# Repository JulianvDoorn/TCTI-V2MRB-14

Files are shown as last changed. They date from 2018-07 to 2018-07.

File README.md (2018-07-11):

# Tri-Servo Platform Practicum
De scope van dit practicum richt zich op het controleren van de positie van een bal in een 2D ruimte. Deze 2D ruimte stelt een plaat voor wat aan de hand van servomotoren kan worden gekanteld. Aan de hand van PID worden de graden berekend en kan er een erg precies systeem worden ontwikkeld.

Het lokaliseren van de bal op de platform zal worden gedaan met gebruik van een webcam. Deze webcam staat op een statief gemonteerd en is haaks op het  _tri-servo platform_  gericht. Dan kan er aan de hand van vision algoritmes de bal worden herkend.

Dit past goed bij de cursus  _Meten, regelen en besturen_, want alle drie de aspecten komen voor in dit practicum. (Meten: vision algoritme, regelen: PID berekening, besturen: servo motoren)

## Functionality
De functionaliteit van de hard- en software staan hieronder beschreven, deze zijn afgeleid uit de MoSCoW requirements in het PvA:

> Cijfers representeren een item uit de must, should and could have. De tientallen representeren de categorie (must, should of could). De eenheden vormen een feature. Voor een werkbaar product is elke feature naar minimaal 'must have' niveau worden gebracht.

-   **21 - Vlugge PID**  PID integratie met een vlugge afstelling, de bal komt snel dichtbij. De steady state error detection (integraal) zal uiteindelijk de laatste correctie doen.
-   **12 - Bal detectie**  Vision algoritme voor bal detectie.
-   **13 - Error bepaling**  Error bepaling op drie assen. Het platform kent drie motoren, dus voor elke motor moet er een error worden bepaald om PID te kunnen regelen.
-   **34 - Automatische beeldafkapping**  Automatische beeldafkapping van de webcam tijdens opstarten.
-   **35 - Automatische motor lokalisatie**  Automatische lokalisering van de motors tijdens opstarten.
-   **26 - Handmatige SetPoint**  Handmatig ingestelde SetPoint, de gebruiker kan op een venster klikken waar de SetPoint is.
-   **17 - Servo aansturing**  Het systeem kan aan de hand van actuators de bal in een richting kunnen bewegen.

## Required Hardware

- 'Tri-Servo Platform'
	- Drie krachtig genoege servomotoren
	- Lichte plaat met lokalisatiestickers (40x40 plexiglas, bijvoorbeeld, liefst ondoorzichtig d.m.v. tape of verf)
	- Elastiek waarmee de plaat in het midden mee wordt gehouden
	- Juiste voeding voor de servomotoren (Wij werkten met een 5V, 0.7A telefoonoplader)
> 5V kan door de Arduino worden geleverd, maar soms trokken de servos te veel stroom, waardoor de Arduino zich resette. Dit is vervelend wanneer je een bal probeert te balanceren.
- Arduino Due
- USB Webcam
	- Statief voor de webcam wat hoog genoeg is om de gehele Tri-Servo Platform in beeld te brengen

### Pin Layout Diagram

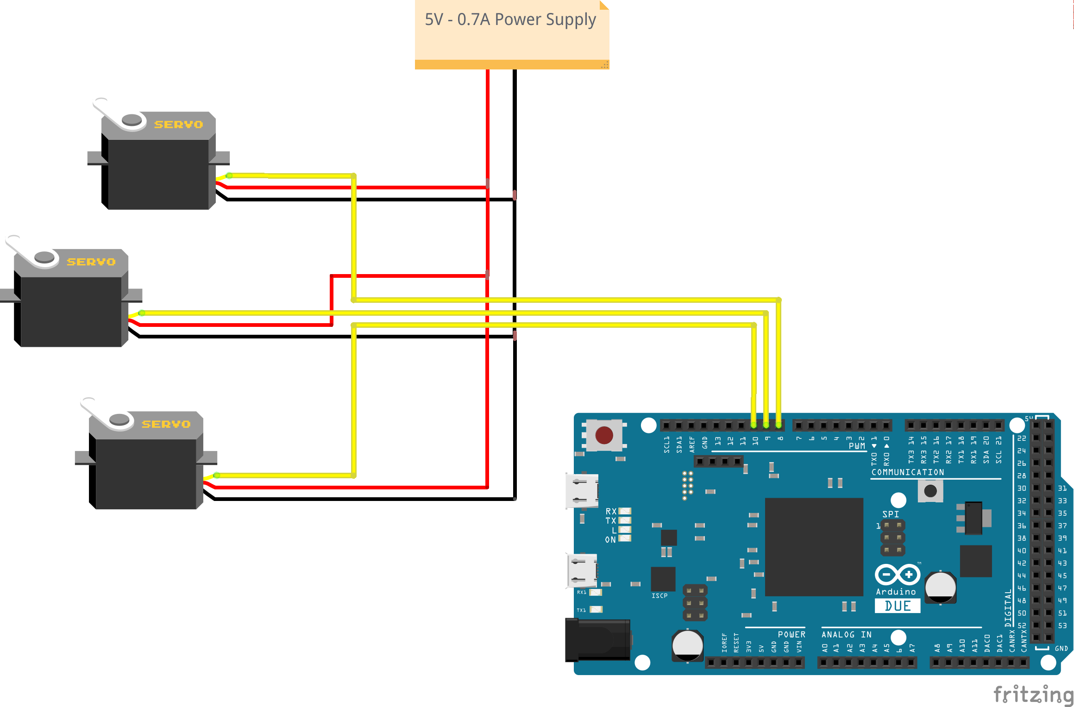
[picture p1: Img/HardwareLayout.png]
Drie Servos en Arduino
<br>
<sub>Pinlayout</sub>

In het bovenstaande diagram staat beschreven hoe de Arduino Due is verbonden met de drie servomotoren en hoe de servomotoren aan de voeding is aangesloten.

Het staat niet gemodelleerd in het schema maar de Arduino krijgt zijn voeding van de PC doormiddel van een USB. Tevens wordt er met deze USB verbinding gecommuniceerd met de PID software. Overigens moet de USB webcam ook aangesloten zijn aan de PC.

## Software dependencies

- Arduino IDE/Toolchain
- Python 3
- OpenCV (voor Python 3)
- Numpy

### Install and user Guide

Wanneer alle hardware gereed staat, kan de software worden geïnstalleerd. De software is doet in principe heel veel zelf wanneer de webcam op het bewegende platform staat gericht. Het is belangrijk dat alle stickers herkenbaar voor de webcam zijn.

#### Vision
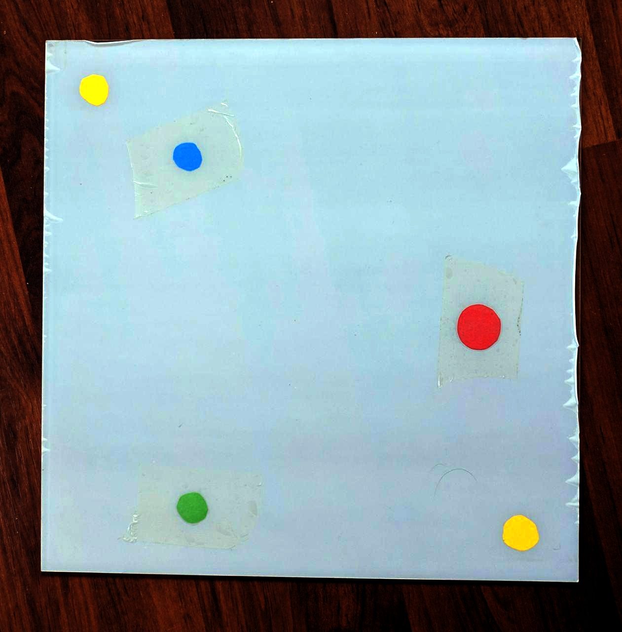
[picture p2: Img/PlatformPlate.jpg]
Platform met stickers
<br>
<sup>Foto van de plaat, hoe de webcam het zou moeten zien</sup>

Dit is hoe onze plaat eruit ziet voor onze webcam. Het is van belang dat de stickers rond zijn en gekleurd in dezelfde kleuren als hierboven. De software filtert namelijk alle kleuren eruit behalve, bijvoorbeeld, rood. Wanneer dit is gedaan voert het stickerherkenning uit. 

De webcam moet verbonden zijn met de 1<sup>e</sup> (niet de 0<sup>e</sup>) virtuele webcam poort. Dit kan in main.py worden aangepast bij `cap = cv2.VideoCapture(1)`. Dit komt omdat de laptop waar het al op was ontwikkeld een webcam op de 0<sup>e</sup> webcam heeft.

#### Arduino
Voordat het allemaal werkt moet eerst nog de Arduino worden geflashed met de code dat de servomotoren aanstuurd aan de hand van seriele commando's. De sketch kan je vinden in het mapje `Arduino/`. Deze sketch kan je met de Arduino IDE uploaden naar je Arduino. Wanneer dit is gedaan heb je de Arduino IDE niet meer nodig.

### Class Diagram

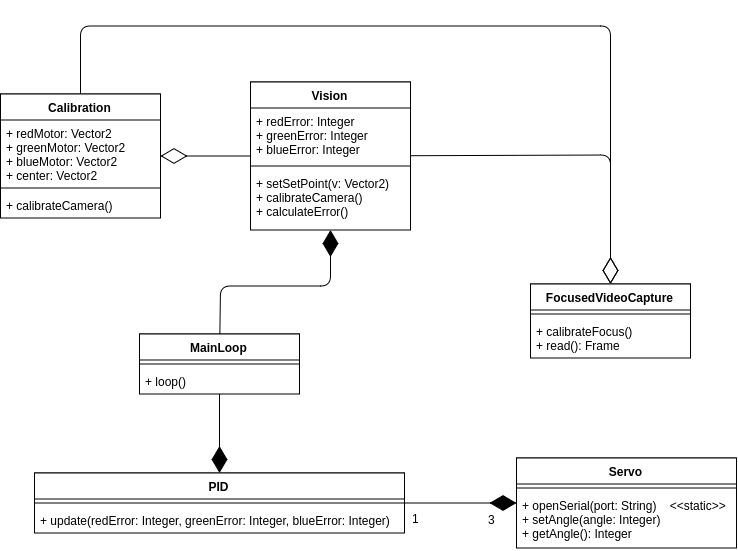
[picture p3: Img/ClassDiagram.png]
Class diagram
<br>
<sup>Klassediagram van de Python software</sup>

| Element | Description |
| :---: |---|
| Vision Class | Dit is het metende gedeelde van het systeem. Het gebruik verschillende algoritmes en een instantie van Calibration om errors te berekenen die bruikbaar zijn voor een PID regelaar. |
| Calibration Class | Bevat subroutines om aan de hand van een video stream de motors te lokaliseren en een middelpunt te berekenen. Wanneer een instantie zich heeft gekalibreerd kan een instantie van Vision gebruik maken van de kalibratie. |
| FocusedVideoCapture Class | Dit is een wrapper class de VideoCapture uit OpenCV. Deze class runt nog een _crop_ operatie over de frame die uit VideoCapture.read() komt. Dit is bruikbaar voor het optimaliseren van de vision algoritmes.  |
| PID Class | Dit is het regelende component van dit systeem. Instances van PID kennen drie servo's en bevat een 'update' functie die de servo's update aan de hand van de ontvangen errors. |
| Servo Class | Dit is het regelende deel van het systeem. Het is gespecialiseerd voor het sturen van commando's naar de Arduino. Elke servo instance bestuurd maar een servo, maar de daadwerkelijke controller kent er maar liefst drie. Daarom moet er de seriële verbinding tussen instances worden gedeeld. Tenzij het geëxpliciteerd is dat verschillende servo's andere seriële poorten gebruiken. |
| MainLoop | In de daadwerkelijke software, is MainLoop niet een class. Maar voor het nut van een class diagram was het belangrijk om dit component de modelleren. Het nut van de MainLoop is om het PID gedeelte en het Vision gedeelte samen te voegen. |

### PID Loop

PID Feedback Loop<br>
<sup>Diagram van de PID feedback lus</sup>

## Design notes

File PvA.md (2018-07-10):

# PvA Tri-Servo Platform Practicum
De scope van dit practicum richt zich op het controleren van de positie van een bal in een 2D ruimte. Deze 2D ruimte stelt een plaat voor wat aan de hand van servomotoren kan worden gekanteld. Aan de hand van PID worden de graden berekend en kan er een erg precies systeem worden ontwikkeld.

Het lokaliseren van de bal op de platform zal worden gedaan met gebruik van een webcam. Deze webcam staat op een statief gemonteerd en is haaks op het _tri-servo platform_ gericht. Dan kan er aan de hand van vision algoritmes de bal worden herkend.

Dit past goed bij de cursus _Meten, regelen en besturen_, want alle drie de aspecten komen voor in dit practicum. (Meten: vision algoritme, regelen: PID berekening, besturen: servo motoren)

## MoSCoW
### Must have
- __11 - Werkbare PID__ PID integratie met werkbare afstelling waarbij de bal uiteindelijk wel op zijn plek komt
- __12 - Bal detectie__ Vision algoritme voor bal detectie.
- __13 - Error bepaling__ Error bepaling op drie assen. Het platform kent drie motoren, dus voor elke motor moet er een error worden bepaald om PID te kunnen regelen.
- __14 - Hardcoded beeldafkapping__ De focus frame van de webcam zit altijd op dezelfde plek. De focus frame zorgt ervoor dat de vision algoritmes optimaal presteren.
- __15 - Hardcoded motor lokalisatie__ Motor posities zitten altijd op dezelfde plek.
- __16 - Hardcoded SetPoint__ Het systeem wilt de bal altijd naar het midden toe brengen.
- __17 - Servo aansturing__ Het systeem moet aan de hand van actuators de bal in een richting kunnen bewegen.
### Should have
- __21 - Vlugge PID__ PID integratie met een vlugge afstelling, de bal komt snel dichtbij. De steady state error detection (integraal) zal uiteindelijk de laatste correctie doen.
- __24 - Handmatige beeldafkapping__ Handmatig ingestelde beeldafkapping van de webcam on de vision algoritmes optimaal te laten werken. Bij opstarten wordt het vlak door de gebruiker ingevoerd.
- __25 - Handmatige motor lokalisatie__ Handmatig ingestelde motor posities relatief aan het focuspunt van de webcam. Bij opstarten worden de punten door de gebruiker ingevoerd.
- __26 - Handmatige SetPoint__ Handmatig ingestelde SetPoint, de gebruiker kan op een venster klikken waar de SetPoint is.
### Could have
- __31 - Perfecte PID__ PID integratie met een onmiddellijke reactie en hoge precisie. De bal word meteen naar de setpoint gebracht en zal geen zichtbare steady state error hebben.
- __34 - Automatische beeldafkapping__ Automatische beeldafkapping van de webcam tijdens opstarten.
- __35 - Automatische motor lokalisatie__ Automatische lokalisering van de motors tijdens opstarten.

## Planning en communicatie
### Planning
Wij vinden dat wij het beste werken aan de hand van een leidraad. Normaliter expliciteren wij die niet op een formele wijze als dit, maar omdat er een schriftelijke PvA moet komen benoemen wij onze leidraad snel.

De volgende tussenproducten willen wij op chronologische wijze opleveren. De items zijn afgeleid van de requirements beschreven bij het kopje MoSCoW (van oud naar nieuw)

##### Must have:
- 14 - Hardcoded beeldafkapping
- 12 - Bal detectie
> Toelichting: als eerste moet er een werkende bal detectie komen. Dit is een cruciaal deel van het regelen van PID. Zonder dit element kan er niks komen dat zelfs op PID lijkt.

- 15 - Hardcoded motor lokalisatie
- 16 - Hardcoded SetPoint
- 13 - Error bepaling
> Toelichting: als tweede moet er een error kunnen worden bepaald. Dit moet dus aan de hand van motor posities en een setpoint. Dan kan er per motor een error worden berekend.

- 17 - Servo aansturing
> Toelichting: voordat de eerste PID kan worden geconfigureerd, moet er een manier zijn om de wereld te beïnvloeden. Dit gaat doormiddel van servomotoren.

- 11 - Werkbare PID
> Toelichting: wanneer er een error bepaling is en servos kunnen worden aangestuurd, kan er een eerste versie van PID kunnen worden geïmplementeerd. 
##### Should have:
- 25 - Handmatige motor lokalisatie
- 24 - Handmatige beeldafkapping
> Toelichting: omdat er een werkbare PID aansturing is, is dit niet meer het hoogste prioriteit. Er kan nu worden gekeken om het calibratieproces te verbeteren om een goede demo te leveren.
- 21 - Vlugge PID
- 26 - Handmatige SetPoint
##### Could have:
- 35 - Automatische motor lokalisatie
- 34 - Automatische beeldafkapping
> Toelichting: als de PID als voldoende wordt geacht, kan er worden gekeken om het calibratieproces te automatiseren. Als dit automatisch is kan er sneller worden getest worden met nieuwe PID waardes.
- 31 - Perfecte PID

### Communicatie
Wij zullen onderhands communiceren doormiddel van Telegram. Hiermee kunnen wij bestanden heen en weer sturen zonder gedoe en kunnen wij snel communiceren tijdens het werken op afstand.
Om met de docent te communiceren zullen wij onze school mails gebruiken en wanneer het uit komt zullen wij de docent persoonlijk opzoeken.

## Risico's
Om dit practicum zo optimaal mogelijk te laten verlopen hebben wij een bepaald aantal risico's in beeld gebracht. Deze risico's gaan in ons geval minder over technische problemen maar over de omstandigheden. Risico's als ziekteverzuim en andere onvoorspelbare kwesties zijn weggelaten.

#### R2D2
Kiet en Julian hebben beiden een verhoogde rol binnen R2D2. Daarom moet er rekening mee geworden dat dit practicum wellicht wordt afgeraffeld vanwege een tekort aan tijd en daarmee onvoldoende te scoren. Het is een optie om te wachten met het inleveren tot na R2D2. Dit zal wel betekenen dat de beoordeling volgens de herkansing gaat, maar het zal dan niet ten koste gaan van het eindcijfer.

Naast R2D2 achten wij dat er geen concrete risico's zijn omtrent dit practicum.

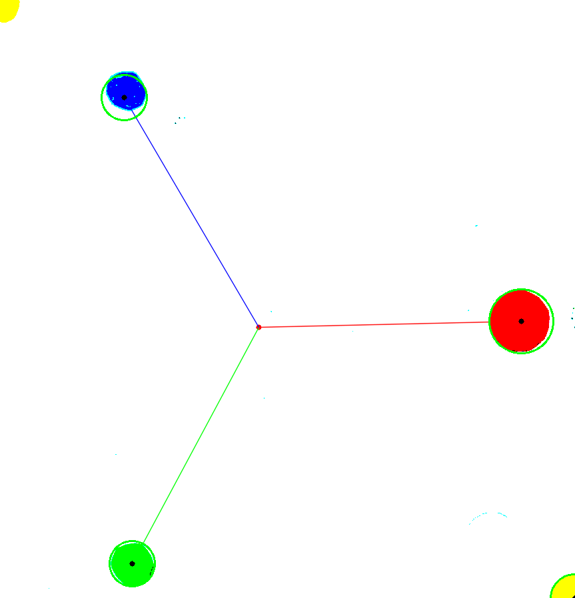
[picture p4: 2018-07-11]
Img/MotorLocalisation.png

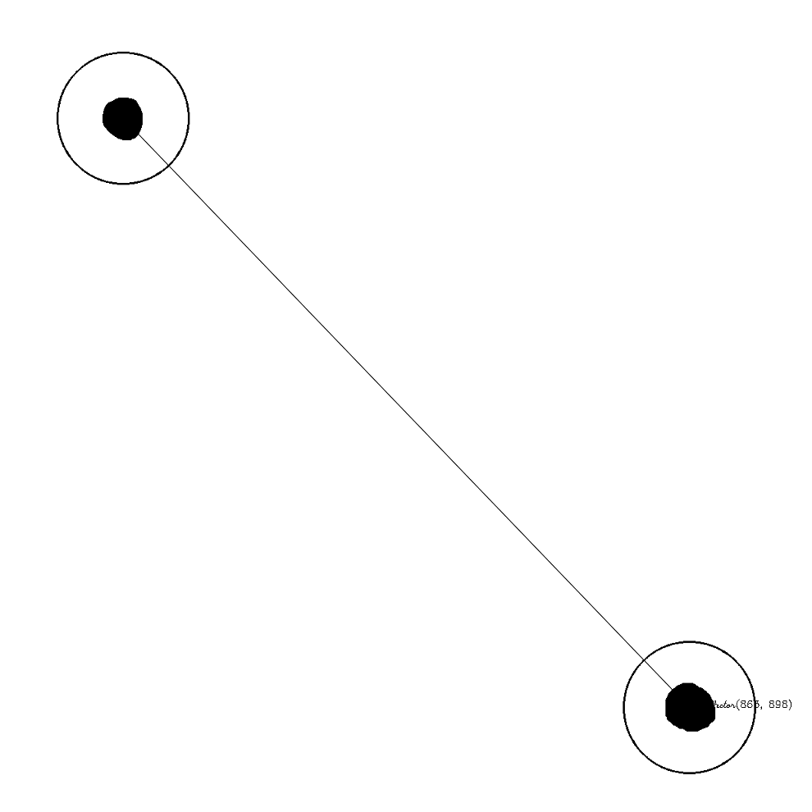
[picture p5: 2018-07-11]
Img/FocusRoutine.png

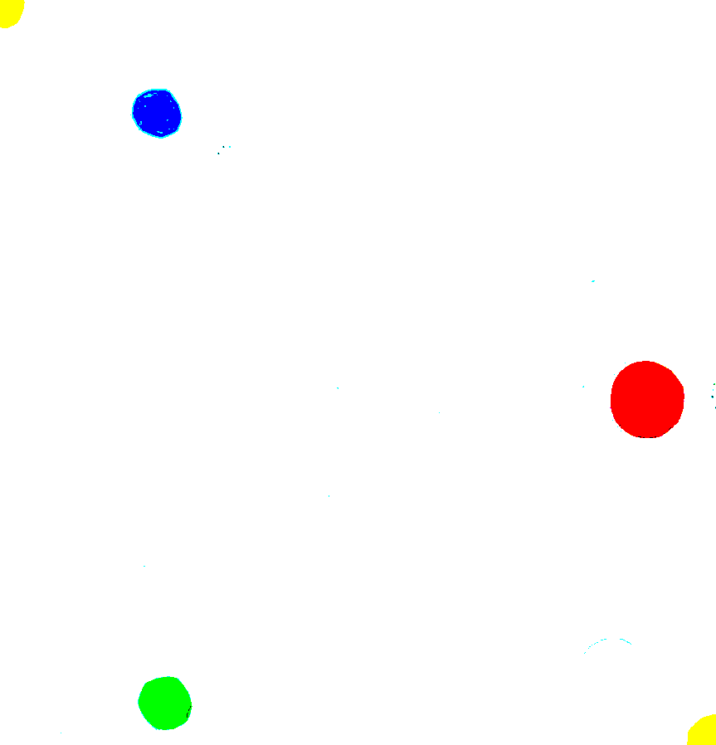
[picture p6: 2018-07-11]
Img/Preprocessed.png

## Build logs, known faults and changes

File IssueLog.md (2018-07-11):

# Issue log
In dit practicum waren er verschillende issues tegengekomen. Problem met bijvoorbeeld dat de bal niet wordt herkend. Of dat de calibratie fout is gelopen
waardoor de software een fout beeld heeft van de realiteit. Kortom, er zijn verschillende problemen gevonden die in de loop van dit practicum zijn op gelost.
In dit document staat er beschreven welke problemen er waren en welke oplossing is gevonden.

Van de volgende opsomming kan er van uit worden gegaan dat de issues in chronologische volgorde zijn geconstateerd en opgelost.

## Resolved issues
### Issue
Er kan geen bal worden herkend op de platform. Het systeem kan dus geen error berekenen.
#### Solution
Doormiddel van een preprocessing filter krijgt een afbeelding een hoog contrast. Wanneer er thresholding op deze afbeelding wordt gedaan springen alle kleuren
eruit en is het makkelijk te identificeren welke kleur waar zit. Maar omdat alleen zwarte elementen in de afbeelding interessant zijn, wordt er een kleuren
filter toegepast. Als een kleur niet dicht genoeg bij zwart zit, wordt de pixel uitgezet, als een kleur erg op zwart lijkt, wordt de pixel aangezet. Op die
manier onstaat er een mask dat over alle zwarte pixels heen gaat. Deze mask is minder gevoelig voor dingen als schaduw en andere laagfrequente gradienten. Op
deze mask kan er blobdetectie worden uitgevoerd. Wanneer er maar een blob in het plaatje zichtbaar is, gaat de software ervan uit dat die blob de bal is.

### Issue
De software kan de gekleurde lokalisatiestickers niet accuraat vinden aan de hand met een kleuren filter en gemiddelde positie van pixels met een specifieke 
kleur. Overigens beinvloeden de stickers elkaar, wanneer bijvoorbeeld een klein beetje groen als blauw wordt gezien. 
#### Solution
Wanneer de gemiddelde positie van bijvoorbeeld een blauwe pixel is bepaald. Kan er een Hough transformatie worden uitgevoerd. Een Hough transformatie
identificeerd alle cirkels op een plaatje, maar bied geen context over deze cirkel. Een mooie oplossing was dus om onze eerste insteek te combineren
met een Hough transformatie. Ons nieuwe algoritme bepaald dus de gemiddelde positie van bijvoorbeeld alle blauwe pixels, vervolgens koppelt hij een
Hough cirkel aan een blob pixels. De blobs bieden dus context aan de preciezere Hough cirkels.

### Issue
Het verschil berekenen tussen twee punten aan de hand van aftrekken en dan pythagoras toepassen geeft geen negatieve waardes terug. Dit is nodig
voor wanneer de bal buiten de drie motor stickers valt, dat moet de PID namelijk ook corrigeren.
#### Solution
In plaats van af te trekken met punten, moeten de setpoint en ballpoint worden geprojecteerd op de as van de servomotor. Aan de hand van deze projectie
kan er ook worden berekend of de bal boven of onder een motor zit. Tevens is deze techniek een stuk beter voor het PID systeem, omdat de error nu meer
de daadwerkelijke acties van de idividuele servomotoren representeerd.

### Issue
Het PID systeem bewoog de plaat op en neer maar hield de plaat nog wel strict horizontaal. Meestal was het gedrag capped out door de servo guard wat ervoor
zorgde dat de servos niks stuk maakten, waardoor het leek alsof het systeem niks meer deed.
#### Solution
De PID class gebruikte voor de opslag van servo specifieke variabelen 'self'. Terwijl PID alle drie de servos onder de controlerende PID class vallen. Alleen
de laatste servo binnen het algoritme deed dus wat hij hoorde te doen, maar de rest deed hetzelfde. Het was opgelost om servo specifieke variabelen onder de
daadwerkelijke servo instanties te brengen, zodat ze niet onterecht worden overschreven.

### Issue
Er moet een hele hoge Kp waarde zijn om de bal in bewegen te laten komen. Dit is op het eerste gezicht niet heel erg, maar dit bracht wel het hele
systeem uit balans omdat de Ki en Kd waardes dan ook anders moesten.
#### Solution
Het probleem had niks met de software te maken. Het zat hem in de hardware van het systeem. Met name de plexiglas en het elastiek dat eronder zat.
het elastiek trok te hard aan de plexiglas waardoor het in een kom werdt gebogen. Het effect is dat er een hoge Kp moet worden ingesteld om de bal uit deze kom
te kunnen laten komen. De oplossing was dus simpelweg het elastiek losser laten zitten. Maar wel strak genoeg om de plaat in het midden te houden.

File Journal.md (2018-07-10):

## Maandag
Hardware opstelling gemaakt, de laatste materialen gekocht zoals een stuk kunststof voor het platform, wat we ook maandag op maat hebben laten klippen. Met behulp van een foto kleuren gedetecteerd voor de verschillende motor punten.

- 9:00 - 10:00: Materialen kopen voor de hardware setup
- 11:00 - 13:00: Hardware setup bouwen
- 13:00 - 16:00: Verschillende kleuren gedetecteerd op een foto

## Dinsdag
Gebruik maken van de webcam en daarmee de keuren van de motoren nog beter detecteren. De berekeningen van de afstanden tussen de punten en daarmee het middel punt van het hele platform. en de projecties van de bal en het setpoint op de lijnen van de motor kleuren naar het middel punt.

- 11:00 - 15:00: Verbeteren van het detecteren van de kleuren en de bal doormiddel van de webcam beelden
- 15:00 - 17:00: Afstanden tussen de motor punten berekenen en de error berekening van de bal ten opzichten van het setpoint

## Woensdag
Code omschrijven naar klasse en logische functies. Gebruik maken van Hough transformatie om cirkels te detecteren en alles nog preciser te maken. De servos aansturen afhankelijk van de afstanden tussen de projectielijnen van de bal en de setpoint op de motorkleurlijnen naar het midden. PID geïmplementeerd

- 10:00 - 12:00: Code opruimen door alles netjes in klasse en functies te plaatsen
- 12:00 - 14:00: Punt detectie verbeten met behulp van haubtransformaties
- 14:00 - 15:00: Aansturen van de servos met seriele verbinding
- 15:00 - 16:00: PID implementeren en de PID waarden setten

## Donderdag
De hardware veranderd zodat de PID beter werkte. Betere PID waardes gekozen. Automatische frame detectie door middel van gele hoeken op de plaat waarmee de nodige grootte van het frame wordt berekent.

- 10:00 - 11:00: Kleine verandering aan de hardware setup om de PID makkelijker te maken
- 11:00 - 12:00: Beter afstellen van de PID
- 12:00 - 14:00: Er voor gezocht dat de focus frame van de webcam automatisch wordt geset en wat laatste verbeteringen aan de vision van de bal

> Totaal aantal uren: 23 uur de man

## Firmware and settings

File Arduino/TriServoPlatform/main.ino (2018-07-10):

// Copyright 2018 Julian van Doorn
// 
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
// The above copyright notice and this permission notice shall be included in all copies or substantial portions of the Software. 
// 
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
#include <Arduino.h>
#include <Servo.h>

#include "triServoPlatform.hpp"
#include "serialDecoder.hpp"

const uint8_t servoLowerBound = 10;
const uint8_t servoUpperBound = 45;
const uint8_t servoNullPosition = 20;

SerialDecoder serialDecoder;
Servo servo0;
Servo servo1;
Servo servo2;
TriServoPlatform triServoPlatform(servo0, servo1, servo2);

/**
 * @brief Sets up the constants required to control the TriServoPlatform
 * 
 * @details
 * Opens a serial connection with a baud rate of 115200 and then attaches three
 * servos to pin 9, 10 and 11. Once the servo controllers are attached to the
 * pins the servos on the TriServoPlatform are set to the servoNullPosition. 
 */
void setup() {
	Serial.begin(115200);
	serialDecoder = SerialDecoder(Serial, triServoPlatform);

	servo0.attach(9, servoLowerBound, servoUpperBound);
	servo1.attach(10, servoLowerBound, servoUpperBound);
	servo2.attach(11, servoLowerBound, servoUpperBound);

	delay(200);

	triServoPlatform.setAngle<0>(servoNullPosition);
	triServoPlatform.setAngle<1>(servoNullPosition);
	triServoPlatform.setAngle<2>(servoNullPosition);
}

/**
 * @brief Calls serialDecoder.loop() every cycle
 */
void loop() {
	serialDecoder.loop();
}

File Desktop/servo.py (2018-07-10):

# Copyright 2018 Julian van Doorn and Kiet van Osnabrugge
#
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
# The above copyright notice and this permission notice shall be included in all copies or substantial portions of the Software.
#
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
from serial import *

from subprocess import call
from sys import platform

## Servo class to control multiple servos using the same serial connection
# @details
# Contains all functionality for opening a serial connection and sending
# commands to the motor controller. Allows for shared serial connections
# among instances. So one Servo instance represents only one servo and it
# does not represent a motor controller hosting multiple servos of any kind
class Servo:
    ## Default serial connection opened by the Serial.__init__ when no serial connection was provided
    defaultSerial = None

    ## Opens a serial connection using the provided port
    # @details
    # This method should be used for opening a serial connection
    # for multiple servo instances to use.
    # @param port Port to use; tty-like for Unix, COM* for Windows
    @staticmethod
    def openSerial(port=None):
        if port is None:
            if platform == "linux" or platform == "linux2":
                port = "/dev/ttyACM0"
            elif platform == "darwin":
                port = "/dev/ttyACM0" # Untested
            elif platform == "win32":
                port = "COM3" # Untested

        serial = Serial(
            port=port,
            baudrate=115200,
            bytesize=EIGHTBITS,
            parity=PARITY_NONE,
            stopbits=STOPBITS_ONE,
            xonxoff=True,
            rtscts=True,
            dsrdtr=False
        )

        if platform == "linux" or platform == "linux2":
            # prevent port from closing every time serial connection is opened
            call(["stty", "-F", port, "-hupcl"])
        elif platform == "darwin":
            pass
            # OS X
            # Undefined behavior for this OS; port may stay open, port may close, should stay open
        elif platform == "win32":
            pass
            # Windows...
            # Undefined behavior for this OS; port may stay open, port may close, should stay open

        return serial

    ## Servo constructor
    # @param motorId Id of the servo motor to control via serial connection
    # @param serial Optional, serial connection to send bytes over, when none provided, a default is used
    def __init__(self, motorId, serial=None, standardOffset=0):
        self.motorId = motorId
        self.standardOffset = standardOffset

        if serial is None:
            if Servo.defaultSerial is None:
                Servo.defaultSerial = Servo.openSerial()
            
            self.serial = Servo.defaultSerial
        else:
            self.serial = serial

        self.angle = None

    ## Sets the angle of the servo with motorId
    # @details
    # Uses the provided serial connection and motorId to communicate with the 
    # servo controlling hardware. The controlling hardware has built-in bounds
    # check so that check is not executed by this function.
    # @param angle Angle to set the servo to
    def setAngle(self, angle):
        data = [0xAA, 0x00, 0x00]

        if self.motorId == 1:
            data[1] = 0x0A
        elif self.motorId == 2:
            data[1] = 0x0B
        elif self.motorId == 3:
            data[1] = 0x0C

        data[2] = angle + self.standardOffset

        self.angle = angle
        self.serial.write(data)

    def getAngle(self):
        return self.angle

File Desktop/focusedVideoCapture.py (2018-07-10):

# Copyright 2018 Julian van Doorn and Kiet van Osnabrugge
#
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
# The above copyright notice and this permission notice shall be included in all copies or substantial portions of the Software.
#
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
import cv2
import util
import numpy as np
from vector import Vector

## OpenCV's VideoCapture class-like with a cropped view
# @details
# Implements a read method which calls the read method of
# the provided OpenCV VideoCapture instance with post-processing
class FocusedVideoCapture:
    ## Constructs a FocusedVideoCapture instance
    # @details
    # Takes all the provided arguments and stores them
    # @param videoCapture OpenCV VideoCapture instance to use as image source
    # @param x X position to crop the frame at
    # @param x Y position to crop the frame at
    # @param w Width of the cropped frame
    # @param h Height of the cropped frame
    def __init__(self, videoCapture, x=None, y=None, w=None, h=None):
        self.videoCapture = videoCapture
        self.x = x
        self.y = y
        self.w = w
        self.h = h

    def calibrateFocus(self):
        frameSizeFound = False
        while not frameSizeFound:
            ret, frame = self.videoCapture.read()

            thresholdedFrame = util.preprocessImage(frame)
            ret, thresholdedFrame =  cv2.threshold(thresholdedFrame,100,255,cv2.THRESH_BINARY)

            thresholdedFrameHSV = cv2.cvtColor(thresholdedFrame, cv2.COLOR_BGR2HSV)

            greenMask = cv2.inRange(thresholdedFrameHSV, np.array([25, 0, 0]), np.array([50, 255, 255]))

            greenMask = cv2.GaussianBlur(greenMask, (5,5), 10)

            kernel = np.ones((5,5),np.uint8)
            erosion = cv2.erode(greenMask, kernel, iterations = 3)
            dilation = cv2.dilate(erosion, kernel, iterations = 3)

            ret, thresholdedFrame = cv2.threshold(dilation, 100, 255, cv2.THRESH_BINARY_INV)

            detector = cv2.SimpleBlobDetector_create()
            keypoints = detector.detect(thresholdedFrame)
            if len(keypoints) == 2:
                point0 = Vector(int(keypoints[0].pt[0]), int(keypoints[0].pt[1]))
                point1 = Vector(int(keypoints[1].pt[0]), int(keypoints[1].pt[1]))
                if point0.values[0] > point1.values[0]:
                    frameSize = point0 - point1
                    self.x = point1.values[0]
                    self.y = point1.values[1]
                else:
                    frameSize = point1 - point0
                    self.x = point0.values[0]
                    self.y = point0.values[1]
                self.w = frameSize.values[0]
                self.h = frameSize.values[1]

                cv2.line(thresholdedFrame, point0.values, point1.values, (0,0,255),1, cv2.LINE_AA)
                cv2.putText(thresholdedFrame, str(frameSize), (point0 + Vector(30, 0)).values, cv2.FONT_HERSHEY_SCRIPT_SIMPLEX, 0.5, (0, 0, 0))

                frameSizeFound = True
            
            for k in keypoints:
                sticker = Vector(int(k.pt[0]), int(k.pt[1]))
                cv2.circle(thresholdedFrame, sticker.values, 100, (0,0,255), 2)
            
            cv2.imshow("Focus calibration", thresholdedFrame)
            

            if cv2.waitKey(1) & 0xFF == ord('q'):
                break

    ## Calls VideoCapture.read() and crops the returned frame
    # @details
    # Calls VideoCapture.read and crops the returned frame. Both the
    # frame and the returned return status is returned to the caller
    # of this method.
    def read(self):
        ret, frame = self.videoCapture.read()
        frame = frame[self.y:self.y+self.h, self.x:self.x+self.w]
        return ret, frame

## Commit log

2018-07-04 Made PID functional
2018-07-04 Removed outdated ball-track.py
2018-07-04 Removed CalibrationData in favor of a tuple
2018-07-04 Wrote doxygen for Calibration, Vision and the util module
    Also renamed some parameters from the util module
2018-07-10 Added debug calibration screen
2018-07-10 Added automatic camera focussing
2018-07-10 Tuned PID parameters to work for our system
2018-07-10 Fixed desktop compatibility with new TriServoPlatform sketch
    [servo.py]
2018-07-10 Fixed missing return statements for operator=
    [serialDecoder.cpp, triServoPlatform.cpp]
2018-07-11 Added hardware layout fritzing diagram
    [HardwareLayout.fzz]
2018-07-11 Fixed issue where calibration wouldn't work with more than 3 hough circles
    [calibration.py]
2018-07-11 Added Img/ folder with more documenting images
    [HardwareLayout.fzz]
2018-07-11 Added breaks between pictures and captions and added caption to pin layout
